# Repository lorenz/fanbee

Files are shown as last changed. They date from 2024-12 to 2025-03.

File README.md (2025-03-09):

# FanBee :honeybee:
*A Zigbee-controlled 140mm fan with electronically-controlled valve*

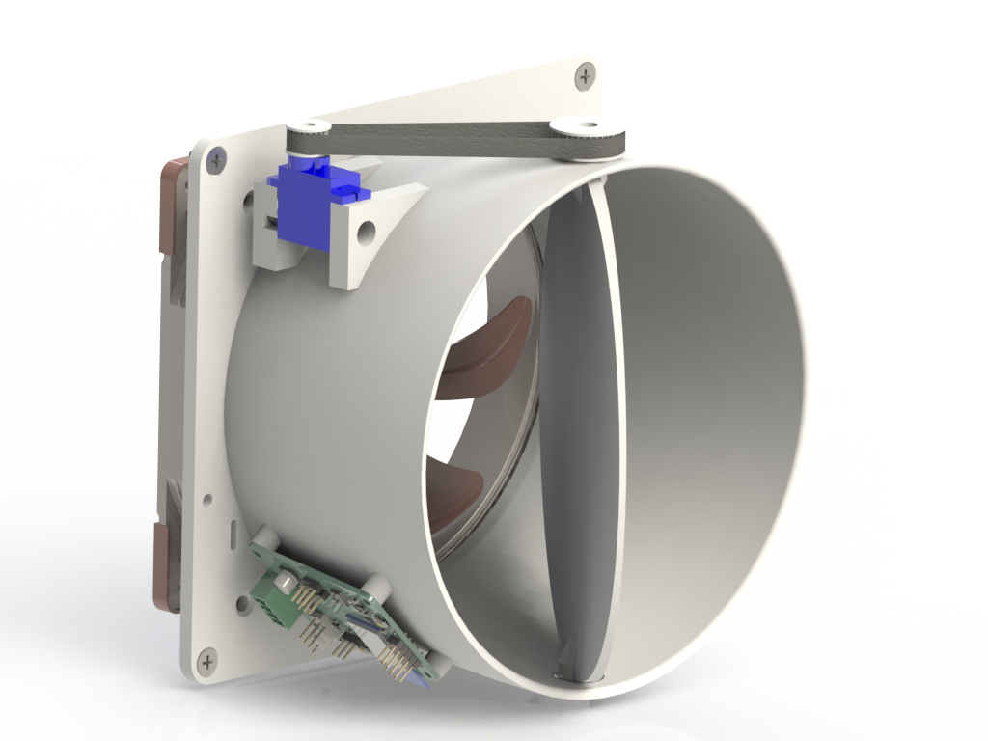
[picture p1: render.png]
Product Picture


Skip to the Build Guide if you want to know how to build one.

# Introduction

## User Interface
The small LED (D3) near the reset button indicates if the lowest (MCU) power
rail has power. If it is not illuminated nothing will happen, check power rails.

The firmware initially starts blinking its status LED (D4, near the JTAG
header) every 2 seconds, indicating that it is idle and is not connected to any
network. Press the Pair button after your ZigBee network is ready to join a new
device. The status LED will start to blink rapidly (every 0.5s) until it has
joined a network, then it will turn off.

Pressing the pair button while the device is already joined to a network will
result in two quick flashes of the status LED.

Long-pressing the pair button (>5s) will reset the device.

The last LED (D5) indicates if the fan is currently powered. It can be used
to diagnose fan or connectivity issues.

## Coordinator compatibility
Because the ZigBee HVAC fan device type is unfit for this device (it supports
various modes but no speed control) I've opted to implement it as a generic
level-controlled device (just like dimmable lights). This should give it fairly
broad coordinator compatibility.

There's a device model for the FanBee in Zigbee2MQTT which is what I'm
personally using to control them.

## Notes
* The power connector is designed for daisy-chaining, that's why there are
  two positive and negative positions. Only one of each needs to be connected
  for normal operation.
* Second Servo output is not used currently, was used in an earlier revision
  and left for any future use as there was space.
* SPI flash can be left unpopulated if you don't ever want to use OTA updates
  or maybe a later (larger) firmware. It's currently unused.
* Newer TI SDKs have been tested but drop off the Zigbee network for unknown
  reasons after hours or days. Use the pinned version.
* Make sure that the surface your're installing the base plate on is flat.
  Otherwise the bell shape gets distorted and the butterfly valve disk gets
  stuck. The tolerances there need to be relatively tight to not allow too much
  air to go through in closed state.

# Build Guide
## Requirements

### Off-the-shelf hardware
| Quantity | Part description |
| --- | --- |
| 8 | M3 brass heat-set inserts |
| 1 | M3 15mm buttonhead fastener |
| 1 | M3 10mm buttonhead fastener |
| 4 | M3 5mm fastener (ideally with integrated washer) |
| 4 | M4 countersunk fasteners for attaching the housing |
| 2 | 10x15x4mm ball bearings |
| 1 | SG90-compatible 180° servo |
| 1 | 140mm 24V or 12V PC-compatible PWM fan (plus screws if not included) |
| 30cm | 2GT timing belt (open-loop) |

This was designed for the Noctua NF-A14 industrialPPC-24V-3000 SP IP67 PWM, but
any other electrically-compatible 24V or 12V fans can be used. Note that the
power supply voltage needs to match the fan voltage, there is no regulator for
the fan power supply.

### PCB
The control PCB is custom-designed and can be ordered at your favorite PCB
manufacturer in various states of assembly. All SMT parts can be assembled
for relatively cheap by JLCPCB. One PCB is needed for each FanBee.

A OpenOCD and JTAG compatible programmer with a 2.45mm ARM 10 Pin JTAG
connector is required. This has been tested with a generic FT2232 board, but
a TI XDS110 or compatible LaunchPad should also work.

### Printed parts
The STLs for all printed parts are in the `parts` folder. One of each is
needed for a single fanbee.
`servo_pulley.stl` should be printed in resin or with a 0.2mm nozzle, the
rest of the parts do not need to be as precise.

## Assembly steps
1. Insert the 4 heat-set inserts into the studs for holding the PCB.
2. Insert the two heat-set inserts into the base for holding an optional PCB enclosure.
3. Insert a heat-set insert each into the bottom and top holes of the valve disk.
4. Press both ball bearings into their housings on the main part.
5. Place the fan at the back, route the wires through the slot and attach it with four fan screws.
6. Route the servo cables through the hole and attach the servo with two screws.
7. Attach the PCB with four 5mm screws.
8. Connect the 4-pin fan connector and 3-pin servo connector.
9. Place the fan disk between the bearings and push in the retaining pin from the bottom and the disk pulley from the top.
10. Secure the retaining pin with the 10mm M3 screw.
11. Secure the disk pulley with the 15mm M3 screw.
12. Push the servo pulley onto the servo and secure it with the provided screw.
13. Cut a sufficiently-long section of belt, loop it around the two servos and secure both ends with the belt retainer.
15. Attach the JTAG programmer and temporary power and flash the firmware.

## Future work
* Public CI for firmware and manufacturing files
* Render/photos of the finished product

# License
MIT for all the code I wrote as well as the CAD design files. Some code is also
related to TI's SimpleLink SDK (especially the generated syscfg), I don't claim
ownership of that, but TI grants you relatively broad permissions for most use.

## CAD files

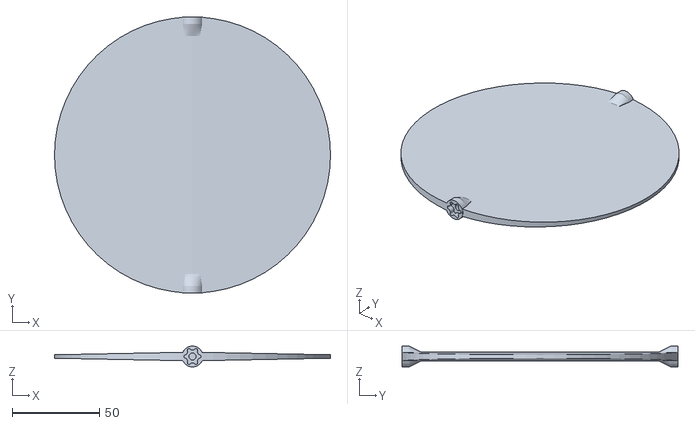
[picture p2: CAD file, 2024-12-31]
parts/valve_disk.stl
158.0 x 158.0 x 12.0

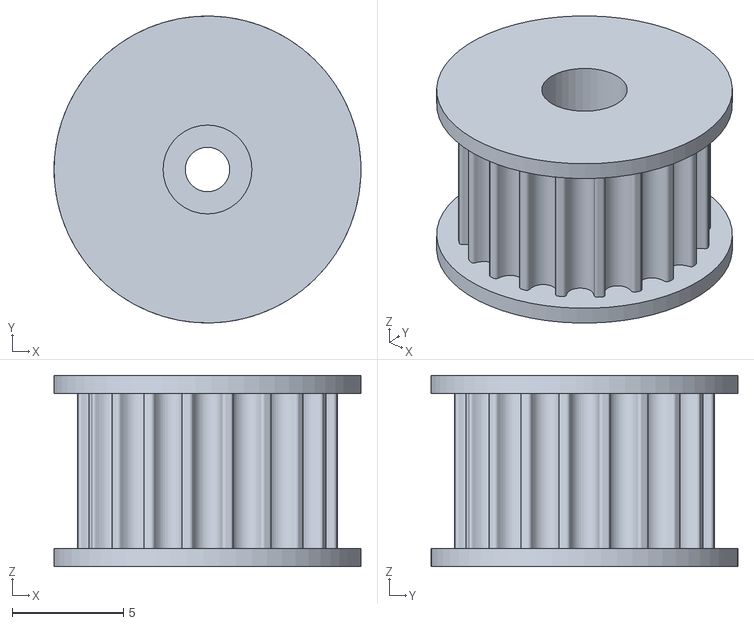
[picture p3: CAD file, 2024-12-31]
parts/servo_pulley.stl
13.8 x 13.8 x 8.60

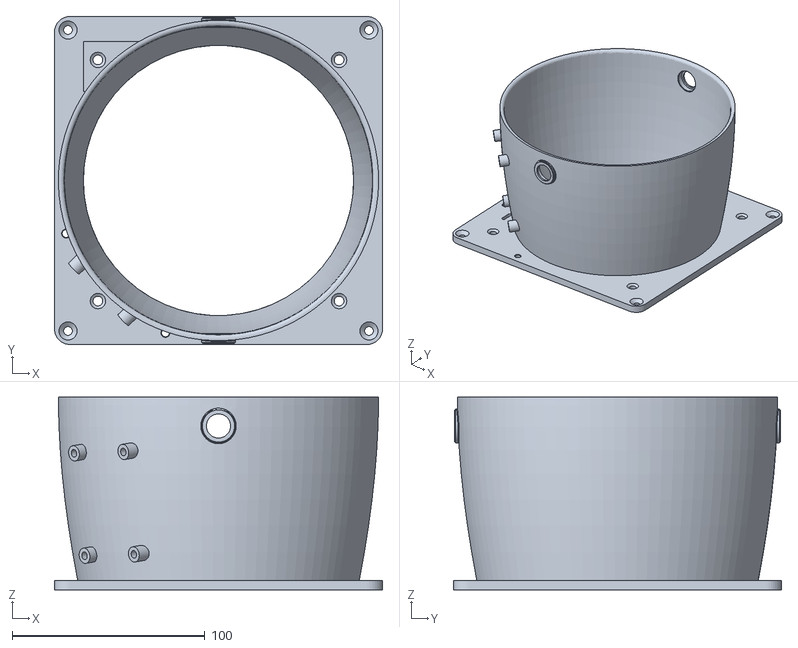
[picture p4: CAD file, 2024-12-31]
parts/housing.stl
170.0 x 170.0 x 100.0

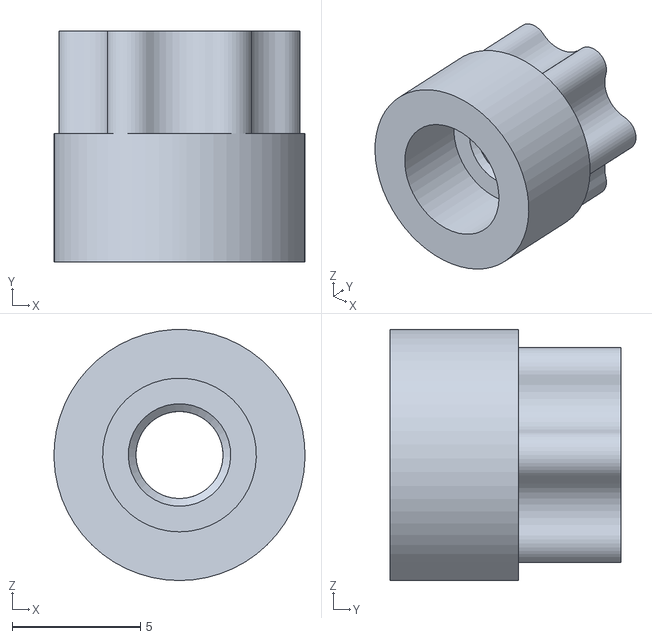
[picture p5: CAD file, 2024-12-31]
parts/retaining_pin.stl
9.80 x 9.00 x 9.80

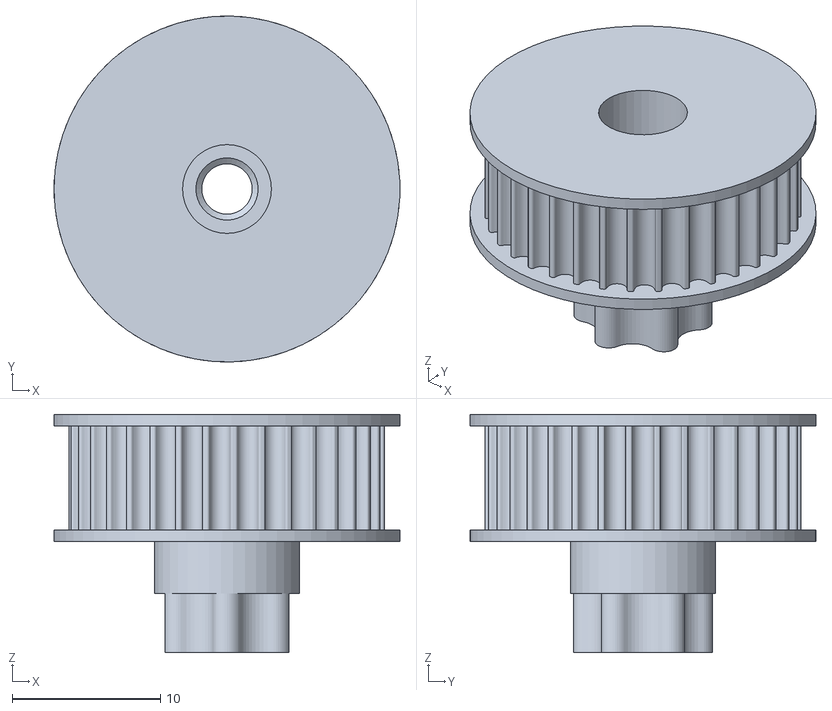
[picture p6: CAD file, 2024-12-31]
parts/disk_pulley.stl
23.4 x 23.4 x 16.1

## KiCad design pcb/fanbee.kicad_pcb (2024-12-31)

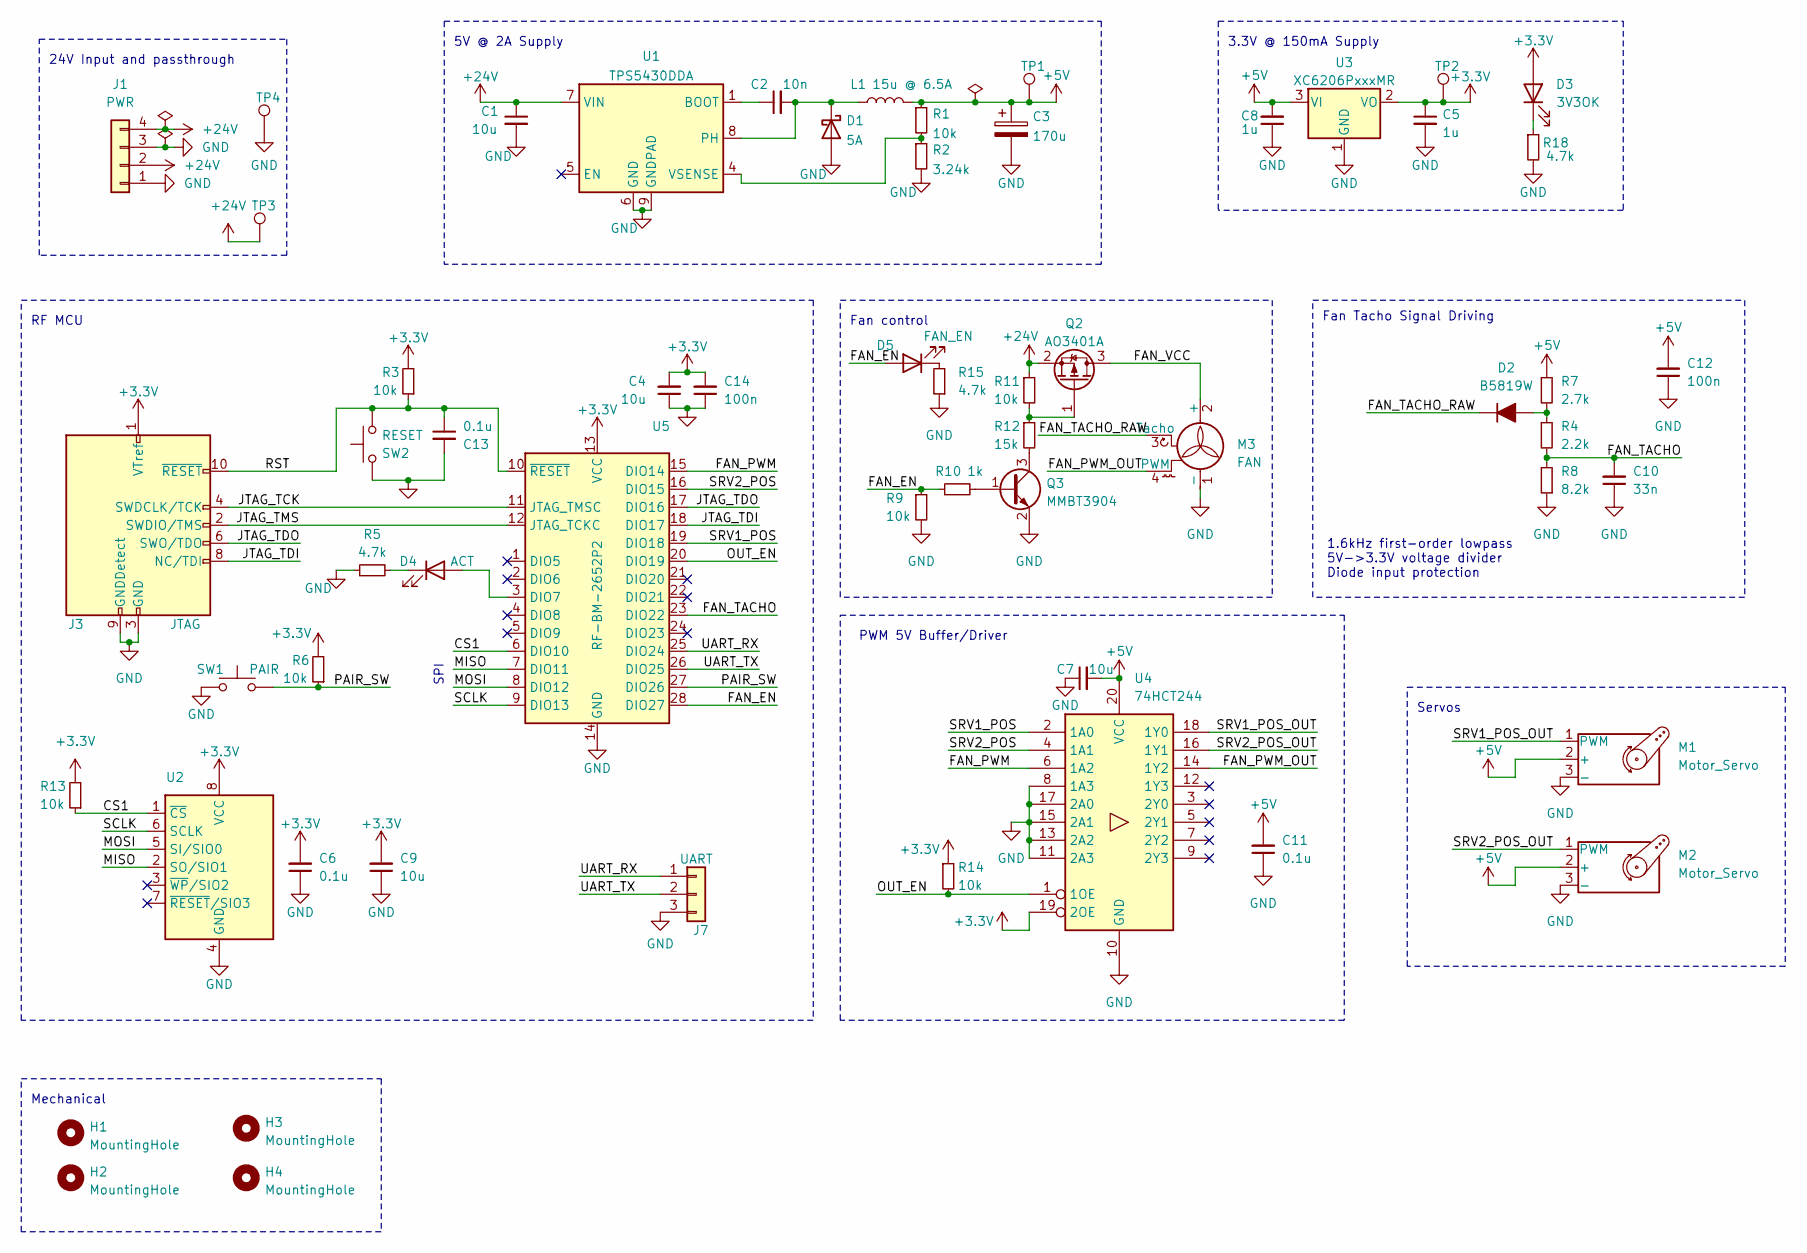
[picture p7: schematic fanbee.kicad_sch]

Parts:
C1, C4, C7, C9: 10u; C_0805_2012Metric; LCSC C440198
C2: 10n; C_0402_1005Metric; LCSC C15195
C3: 170u; CP_Elec_6.3x5.9; LCSC C311623
C5, C8: 1u; C_0805_2012Metric; LCSC C28323
C6, C11, C13: 0.1u; C_0402_1005Metric; LCSC C1525
C10: 33n; C_0603_1608Metric; LCSC C21117
C12, C14: 100n; C_0603_1608Metric; LCSC C14663
D1: 5A; D_SMA; LCSC C22452
D2: B5819W; D_SOD-123; LCSC C8598
D3: 3V3OK; LED_0805_2012Metric; LCSC C2297
D4: ACT; LED_0805_2012Metric; LCSC C2297
D5: FAN_EN; LED_0805_2012Metric; LCSC C2297
H1, H2, H3, H4: MountingHole; MountingHole_3.2mm_M3
J1: PWR; PhoenixContact_MCV_1,5_4-G-3.81_1x04_P3.81mm_Vertical; LCSC C8410
J3: JTAG; PinHeader_2x05_P2.54mm_Vertical; LCSC C7501276
J7: UART; PinHeader_1x03_P2.54mm_Vertical; LCSC C7501581
L1: 15u @ 6.5A; L_Sunlord_MWSA1004_11.5x10.5mm; LCSC C151872
M1, M2: Motor_Servo; PinHeader_1x03_P2.54mm_Vertical; LCSC C7501581
M3: FAN; FanPinHeader_1x04_P2.54mm_Vertical; LCSC C7501582
Q2: AO3401A; SOT-23; LCSC C15127
Q3: MMBT3904; SOT-23; LCSC C20526
R1, R3, R6, R9, R11, R13, R14: 10k; R_0402_1005Metric; LCSC C25744
R2: 3.24k; R_0402_1005Metric; LCSC C22994
R4: 2.2k; R_0402_1005Metric; LCSC C25879
R5, R15, R18: 4.7k; R_0402_1005Metric; LCSC C25900
R7: 2.7k; R_0603_1608Metric; LCSC C13167
R8: 8.2k; R_0402_1005Metric; LCSC C25924
R10: 1k; R_0402_1005Metric; LCSC C11702
R12: 15k; R_0402_1005Metric; LCSC C25756
SW1: PAIR; SW_SPST_TL3342; LCSC C318884
SW2: RESET; SW_SPST_TL3342; LCSC C318884
TP1, TP2, TP3, TP4: TestPoint; TestPoint_Pad_D1.0mm
U1: TPS5430DDA; TI_SO-PowerPAD-8_ThermalVias; LCSC C9864
U2: Macronix_USON8_EP_2x3_Pitch0.5mm; LCSC C152596
U3: XC6206PxxxMR; SOT-23-3; LCSC C5446
U4: 74HCT244; TSSOP-20_4.4x6.5mm_P0.65mm; LCSC C131088
U5: RF-BM-2652P2; LCSC C5440064

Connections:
+3.3V: C4.2, C5.1, C6.2, C9.2, C14.2, D3.2 (A), J3.1 (VTref), R3.2, R6.2, R13.2, R14.1, TP2.1, U2.8 (VCC), U3.2 (VO), U4.19 (2OE), U5.13 (VCC)
+5V: C3.1, C7.2, C8.2, C11.2, C12.2, L1.2, M1.2 (+), M2.2 (+), R1.1, R7.1, TP1.1, U3.3 (VI), U4.20 (VCC)
+24V: C1.1, J1.2, J1.4, Q2.2 (S), R11.1, TP3.1, U1.7 (VIN)
/CS1: R13.1, U2.1 (~CS), U5.6 (DIO10)
/FAN_EN: D5.2 (A), R9.1, R10.1, U5.28 (DIO27)
/FAN_PWM: U4.6 (1A2), U5.15 (DIO14)
/FAN_PWM_OUT: M3.4 (PWM), U4.14 (1Y2)
/FAN_TACHO: C10.2, R4.2, R8.2, U5.23 (DIO22)
/FAN_TACHO_RAW: D2.1 (K), M3.3 (Tacho)
/FAN_VCC: M3.2 (+), Q2.3 (D)
/JTAG_TCK: J3.4 (SWDCLK/TCK), U5.11 (JTAG_TMSC)
/JTAG_TDI: J3.8 (NC/TDI), U5.18 (DIO17)
/JTAG_TDO: J3.6 (SWO/TDO), U5.17 (DIO16)
/JTAG_TMS: J3.2 (SWDIO/TMS), U5.12 (JTAG_TCKC)
/MISO: U2.2 (SO/SIO1), U5.7 (DIO11)
/MOSI: U2.5 (SI/SIO0), U5.8 (DIO12)
/OUT_EN: R14.2, U4.1 (1OE), U5.20 (DIO19)
/PAIR_SW: R6.1, SW1.2, U5.27 (DIO26)
/RST: C13.1, J3.10 (~RESET), R3.1, SW2.1, U5.10 (~RESET)
/SCLK: U2.6 (SCLK), U5.9 (DIO13)
/SRV1_POS: U4.2 (1A0), U5.19 (DIO18)
/SRV1_POS_OUT: M1.1 (PWM), U4.18 (1Y0)
/SRV2_POS: U4.4 (1A1), U5.16 (DIO15)
/SRV2_POS_OUT: M2.1 (PWM), U4.16 (1Y1)
/UART_RX: J7.1, U5.25 (DIO24)
/UART_TX: J7.2, U5.26 (DIO25)
GND: C1.2, C3.2, C4.1, C5.2, C6.1, C7.1, C8.1, C9.1, C10.1, C11.1, C12.1, C13.2, C14.1, D1.2 (A), J1.1, J1.3, J3.3 (GND), J3.5 (GND), J3.9 (GNDDetect), J7.3, M1.3 (-), M2.3 (-), M3.1 (-), Q3.2 (E), R2.2, R5.1, R8.1, R9.2, R15.1, R18.2, SW1.1, SW2.2, TP4.1, U1.6 (GND), U1.9 (GNDPAD), U2.4 (GND), U2.EP (GND), U3.1 (GND), U4.8 (1A3), U4.10 (GND), U4.11 (2A3), U4.13 (2A2), U4.15 (2A1), U4.17 (2A0), U5.14 (GND)
unnamed: C2.2, D1.1 (K), L1.1, U1.8 (PH)
unnamed: D2.2 (A), R4.1, R7.2
unnamed: D3.1 (K), R18.1
unnamed: D4.2 (A), U5.3 (DIO7)
unnamed: D4.1 (K), R5.2
unnamed: D5.1 (K), R15.2
unnamed: Q2.1 (G), R11.2, R12.1
unnamed: Q3.1 (B), R10.2
unnamed: Q3.3 (C), R12.2
unnamed: C2.1, U1.1 (BOOT)
unnamed: R1.2, R2.1, U1.4 (VSENSE)

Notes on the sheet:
1.6kHz first-order lowpass 5V->3.3V voltage divider Diode input protection
RF MCU
SPI
Mechanical
Servos
5V @ 2A Supply
Fan Tacho Signal Driving
PWM 5V Buffer/Driver
24V Input and passthrough
Fan control
3.3V @ 150mA Supply

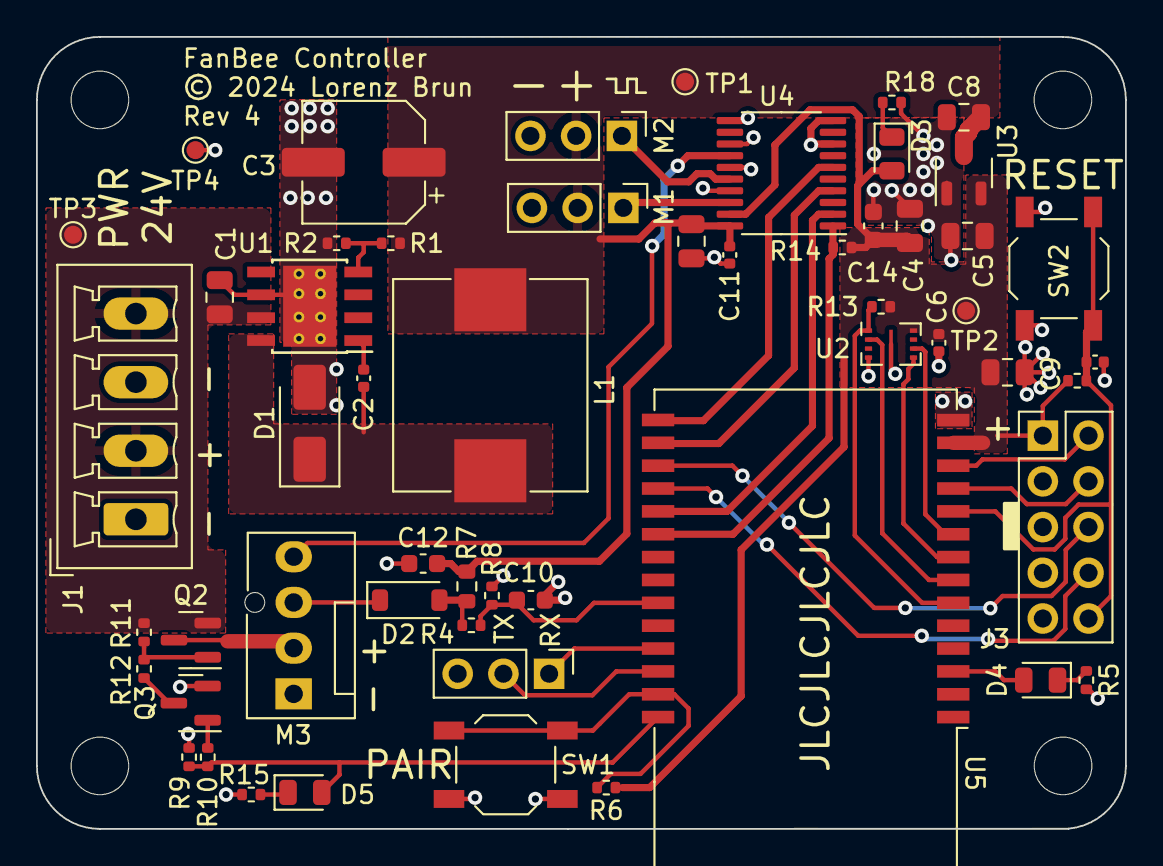
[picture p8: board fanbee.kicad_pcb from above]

Board: 2 copper layers, 60.5 x 44.0 mm, 59 parts (0 on the bottom side), 38 nets.

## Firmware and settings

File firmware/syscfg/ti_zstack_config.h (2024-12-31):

/*
 * Copyright (c) 2018, Texas Instruments Incorporated
 * All rights reserved.
 *
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
 * *  Redistributions of source code must retain the above copyright
 *    notice, this list of conditions and the following disclaimer.
 *
 * *  Redistributions in binary form must reproduce the above copyright
 *    notice, this list of conditions and the following disclaimer in the
 *    documentation and/or other materials provided with the distribution.
 *
 * *  Neither the name of Texas Instruments Incorporated nor the names of
 *    its contributors may be used to endorse or promote products derived
 *    from this software without specific prior written permission.
 *
 * THIS SOFTWARE IS PROVIDED BY THE COPYRIGHT HOLDERS AND CONTRIBUTORS "AS IS"
 * AND ANY EXPRESS OR IMPLIED WARRANTIES, INCLUDING, BUT NOT LIMITED TO,
 * THE IMPLIED WARRANTIES OF MERCHANTABILITY AND FITNESS FOR A PARTICULAR
 * PURPOSE ARE DISCLAIMED. IN NO EVENT SHALL THE COPYRIGHT OWNER OR
 * CONTRIBUTORS BE LIABLE FOR ANY DIRECT, INDIRECT, INCIDENTAL, SPECIAL,
 * EXEMPLARY, OR CONSEQUENTIAL DAMAGES (INCLUDING, BUT NOT LIMITED TO,
 * PROCUREMENT OF SUBSTITUTE GOODS OR SERVICES; LOSS OF USE, DATA, OR PROFITS;
 * OR BUSINESS INTERRUPTION) HOWEVER CAUSED AND ON ANY THEORY OF LIABILITY,
 * WHETHER IN CONTRACT, STRICT LIABILITY, OR TORT (INCLUDING NEGLIGENCE OR
 * OTHERWISE) ARISING IN ANY WAY OUT OF THE USE OF THIS SOFTWARE,
 * EVEN IF ADVISED OF THE POSSIBILITY OF SUCH DAMAGE.
 *
 */

/*
 *                           ti_zstack_config.h
 *
 *  DO NOT EDIT - This file was generated by the SysConfig tool.
 *
 *  Macros used to define a TI Z-Stack ZigBee device. New user defined
 *  options may be added to this file, as necessary.
 *
 */

#ifndef TI_ZSTACK_CONFIG_H
#define TI_ZSTACK_CONFIG_H

/* Default (primary) and secondary channel masks. Secondary mask is used when the
 * default channels fail.
 * Channels are defined in the following:
 *        11 - 26 : 2.4 GHz     0x07FFF800
 */
#ifndef DEFAULT_CHANLIST
#define DEFAULT_CHANLIST              0x02108800
#endif

#ifndef SECONDARY_CHANLIST
#define SECONDARY_CHANLIST            0x05ef7000
#endif

/* Define the default PAN ID.
 *
 * Setting this to a value other than 0xFFFF causes
 * ZDO_COORD to use this value as its PAN ID and
 * Routers and end devices to join PAN with this ID
 */
#ifndef ZDAPP_CONFIG_PAN_ID
#define ZDAPP_CONFIG_PAN_ID           0xFFFF
#endif

/* Specifiy whether to set the EPID to the Extended Address, or to use the
 * custom Extended Pan ID (EPID) defined by ZDAPP_CONFIG_EPID
 */
#ifndef SET_EPID_AS_EXT_ADDR
#define SET_EPID_AS_EXT_ADDR          TRUE
#endif

/* Define the default Extended Pan ID (EPID)
 * ZDAPP_CONFIG_EPID is only used if SET_EPID_AS_EXT_ADDR is FALSE. Otherwise,
 * the EPID is set to the Extended Address.
 */
#ifndef ZDAPP_CONFIG_EPID
#define ZDAPP_CONFIG_EPID             {0x01,0x23,0x45,0x67,0x89,0xAB,0xCD,0xEF}
#endif

/* in seconds; set to 255 to turn off route expiry */
#ifndef ROUTE_EXPIRY_TIME
#define ROUTE_EXPIRY_TIME             30
#endif

/*  Default indirect message holding timeout value:
 *  1-65535 (0 -> 65536) X CNT_RTG_TIMER X RTG_TIMER_INTERVAL
 */
#ifndef NWK_INDIRECT_MSG_TIMEOUT
#define NWK_INDIRECT_MSG_TIMEOUT      7
#endif

/* The number of simultaneous route discoveries in network */
#ifndef MAX_RREQ_ENTRIES
#define MAX_RREQ_ENTRIES              8
#endif

/* The maximum number of MAC frame transmission attempts allowed */
#ifndef ZMAC_MAX_FRAME_RETRIES
#define ZMAC_MAX_FRAME_RETRIES          3
#endif

/* Max number of times attempts looking for the next hop address of a message */
#ifndef NWK_MAX_DATA_RETRIES
#define NWK_MAX_DATA_RETRIES          2
#endif

/* The maximum number of times APS frames are retried after not receiving an APS ACK */
#ifndef APSC_MAX_FRAME_RETRIES
#define APSC_MAX_FRAME_RETRIES        3
#endif

/* This number is used by polled devices, since the spec'd formula
 * doesn't work for sleeping end devices.  For non-polled devices,
 * a formula is used. Value is in 2 milliseconds periods
 */
#ifndef APSC_ACK_WAIT_DURATION_POLLED
#define APSC_ACK_WAIT_DURATION_POLLED 3000
#endif

/* The maximum number of groups in the groups table */
#ifndef APS_MAX_GROUPS
#define APS_MAX_GROUPS                16
#endif

/* Number of entries in the regular routing table plus additional
 * entries for route repair
 */
#ifndef MAX_RTG_ENTRIES
#define MAX_RTG_ENTRIES               40
#endif

/* Maximum number of entries in the Binding table. */
#ifndef NWK_MAX_BINDING_ENTRIES
#define NWK_MAX_BINDING_ENTRIES       4
#endif

/* Default security key. */
#ifndef DEFAULT_KEY
#define DEFAULT_KEY                   {0x00,0x00,0x00,0x00,0x00,0x00,0x00,0x00,0x00,0x00,0x00,0x00,0x00,0x00,0x00,0x00}
#endif

/* ZigBee Alliance Pre-configured Distributed Link Key (for Distributed networks) */
#ifndef DISTRIBUTED_GLOBAL_LINK_KEY
#define DISTRIBUTED_GLOBAL_LINK_KEY   {0xD0,0xD1,0xD2,0xD3,0xD4,0xD5,0xD6,0xD7,0xD8,0xD9,0xDA,0xDB,0xDC,0xDD,0xDE,0xDF}
#endif

/* ZigBee Alliance Pre-configured TC Link Key - 'ZigBeeAlliance09' (for Centralized networks) */
#ifndef DEFAULT_TC_LINK_KEY
#define DEFAULT_TC_LINK_KEY           {0x5a,0x69,0x67,0x42,0x65,0x65,0x41,0x6c,0x6c,0x69,0x61,0x6e,0x63,0x65,0x30,0x39}
#endif

/* The number of milliseconds to wait between data request polls to the coordinator. */
#ifndef TXPOWER
#define TXPOWER                     15
#endif

/****************************************
 * The following are for End Devices only
 ***************************************/

/* Determine whether the radio on an End Device is always on */
#ifndef RFD_RX_ALWAYS_ON_CAPABLE
#define RFD_RX_ALWAYS_ON_CAPABLE            TRUE
#endif

#ifndef RFD_RX_ALWAYS_ON
#define RFD_RX_ALWAYS_ON                    TRUE
#endif

/* The minimum poll rate. */
#ifndef MINIMUM_APP_POLL_RATE
#define MINIMUM_APP_POLL_RATE                     100
#endif

/* The number of milliseconds to wait between data request polls to the coordinator. */
#ifndef POLL_RATE
#define POLL_RATE                     3000
#endif

/* This is used after receiving a data indication to poll immediately
 * for queued messages...in milliseconds.
 */
#ifndef QUEUED_POLL_RATE
#define QUEUED_POLL_RATE              100
#endif

/* This is used after receiving a data confirmation to poll immediately
 * for response messages...in milliseconds
 */
#ifndef RESPONSE_POLL_RATE
#define RESPONSE_POLL_RATE            100
#endif

/* This is used as an alternate response poll rate only for rejoin request.
 * This rate is determined by the response time of the parent that the device
 * is trying to join.
 */
#ifndef REJOIN_POLL_RATE
#define REJOIN_POLL_RATE              440
#endif

/* Maximum number of devices in the Assoc/Device list. */
#ifndef NWK_MAX_DEVICE_LIST
#define NWK_MAX_DEVICE_LIST           20
#endif

/* Total Number of APS keys that a TC can manage. This is equal to the number of devices a ZC can allow to join the network */
#ifndef ZDSECMGR_TC_DEVICE_MAX
#define ZDSECMGR_TC_DEVICE_MAX        3
#endif

/* Value used by end device when sending End Device Timeout Request */
/* This is an index into table timeoutValue[] defined in nwk_globals.c */
#ifndef END_DEV_TIMEOUT_VALUE
#define END_DEV_TIMEOUT_VALUE        8
#endif





/* Maximum size in bytes used by reportable attributes registered in any endpoint for the application (for analog attributes) */
#ifndef BDBREPORTING_MAX_ANALOG_ATTR_SIZE
#define BDBREPORTING_MAX_ANALOG_ATTR_SIZE                   4
#endif

/* Cluster Flags */
#define ZCL_SYSCONFIG
#define ZCL_READ
#define ZCL_WRITE
#define ZCL_DISCOVER
#define ZCL_BASIC
#define ZCL_IDENTIFY
#define ZCL_GROUPS
#define ZCL_SCENES
#define ZCL_ON_OFF
#define ZCL_LEVEL_CTRL
#define BDB_REPORTING


#endif /* TI_ZSTACK_CONFIG_H */

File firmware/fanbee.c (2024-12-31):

#include "fanbee.h"

#include <stdint.h>
#include <string.h>
#include <ti/display/Display.h>
#include <ti/drivers/NVS.h>
#include <ti/drivers/apps/Button.h>
#include <ti/sysbios/BIOS.h>
#include <ti/sysbios/family/arm/cc26xx/Timer.h>
#include <ti/sysbios/knl/Clock.h>
#include <ti/sysbios/knl/Semaphore.h>
#include <ti/sysbios/knl/Task.h>

#include "bdb_interface.h"
#include "cui.h"
#include "gp_common.h"
#include "nvintf.h"
#include "ota_client.h"
#include "ti_drivers_config.h"
#include "util_timer.h"
#include "zcl_config.h"
#include "zcl_ota.h"
#include "zcl_port.h"
#include "zcomdef.h"
#include "zstackapi.h"
#include "zstackmsg.h"

uint8 fanbee_Basic_ManufacturerName[] = {11, 'L', 'o', 'r', 'e', 'n', 'z', ' ', 'B', 'r', 'u', 'n'};
uint8 fanbee_Basic_ModelIdentifier[] = {7, 'F', 'a', 'n', 'B', 'e', 'e', '1'};
const enum8 DEFAULT_FANBEE_BASIC_POWER_SOURCE = POWER_SOURCE_DC;
const uint8 DEFAULT_FANBEE_LEVEL_CURRENT_LEVEL = 254;

// Semaphore used to post events to the application thread
static Semaphore_Handle appSemHandle;
static Semaphore_Struct appSem;

// App service ID used for messaging with stack service task
uint8_t sampleApp_serviceTaskId;

// App service task events, set by the stack service task when sending a message
static uint32_t appServiceTaskEvents;

// Passed in function pointers to the NV driver
static NVINTF_nvFuncts_t *nvm = NULL;

// Constants (TODO: Determine)
static const uint32_t valve_open = 2300;
static const uint32_t valve_closed = 600;

// Peripheral handles
static Display_Handle debug_display_handle;

static Button_Handle pair_btn_handle;

static LED_Handle act_led_handle;

static Clock_Handle tacho_clk_handle;
static Clock_Struct tacho_clk_struct;

static PWM_Handle pwm_fan = NULL;

static PWM_Handle pwm_srv1 = NULL, pwm_srv2 = NULL;

static bool joined = false;

// Functions for sample application setup
void sampleApp_task(NVINTF_nvFuncts_t *pfnNV);
static void fanbee_process_loop();
static void fanbee_initPeripherals();
static void fanbee_processZStackMsgs(zstackmsg_genericReq_t *pMsg);
static void fanbee_processAfIncomingMsgInd(zstack_afIncomingMsgInd_t *pInMsg);
static void fanbee_initZCLGeneral();
static void fanbee_ProcessCommissioningStatus(bdbCommissioningModeMsg_t *bdbCommissioningModeMsg);

// Update hooks
static void fanbee_updateOutputs();
static void fanbee_updateLevel();
static void fanbee_updateOnOff();

// Functions to process ZCL Foundation incoming Command/Response messages
static uint8_t fanbee_ProcessIncomingMsg(zclIncoming_t *pInMsg);

void Board_initHook(void) { PWM_init(); }

static NVINTF_itemID_t nvOnOffId = {
    .systemID = NVINTF_SYSID_APP,
    .itemID = FANBEE_NV_ONOFF,
    .subID = 0,
};
static NVINTF_itemID_t nvCurrentLevelId = {
    .systemID = NVINTF_SYSID_APP,
    .itemID = FANBEE_NV_CURRENT_LEVEL,
    .subID = 0,
};

// Application task entry point
void sampleApp_task(NVINTF_nvFuncts_t *pfnNV) {
  // Save and register the function pointers to the NV drivers
  nvm = pfnNV;
  if (nvm == NULL) {
    Display_printf(debug_display_handle, 0, 0, "No NVM available");
  }
  zclport_registerNV(nvm, ZCL_PORT_SCENE_TABLE_NV_ID);

  // Create semaphores for messages / events
  Semaphore_Params semParam;
  Semaphore_Params_init(&semParam);
  semParam.mode = ti_sysbios_knl_Semaphore_Mode_COUNTING;
  appSemHandle = Semaphore_construct(&appSem, 0, &semParam);
  sampleApp_serviceTaskId = OsalPort_registerTask(Task_self(), appSemHandle, &appServiceTaskEvents);

  fanbee_initPeripherals();

  // Initialize Zigbee
  fanbee_initZCLGeneral();
  gp_endpointInit(sampleApp_serviceTaskId);
  app_Green_Power_Init(sampleApp_serviceTaskId, &appServiceTaskEvents, appSemHandle,
                       FANBEE_GP_DATA_SEND_EVT, FANBEE_GP_EXPIRE_DUPLICATE_EVT,
                       FANBEE_GP_TEMP_MASTER_EVT);

  uint32_t onOffErr = NVINTF_NOTFOUND;
  uint32_t levelErr = NVINTF_NOTFOUND;
  if (nvm->readItem) {
    nvm->readItem(nvCurrentLevelId, 0, sizeof(fanbee_Level_CurrentLevel),
                  &fanbee_Level_CurrentLevel);
    nvm->readItem(nvOnOffId, 0, sizeof(fanbee_OnOff_OnOff), &fanbee_OnOff_OnOff);
  }

  if ((onOffErr == NVINTF_NOTFOUND) && nvm->createItem) {
    nvm->createItem(nvOnOffId, sizeof(fanbee_OnOff_OnOff), &fanbee_OnOff_OnOff);
  }
  if ((levelErr == NVINTF_NOTFOUND) && nvm->createItem) {
    nvm->createItem(nvCurrentLevelId, sizeof(fanbee_Level_CurrentLevel),
                    &fanbee_Level_CurrentLevel);
  }

  // Set up output state
  fanbee_updateOutputs();

  // Enable line driver IC outputs.
  GPIO_write(CONFIG_DRV_EN, 1);

  Display_printf(debug_display_handle, 0, 0, "Init done, starting loop");

  // No return from task process
  fanbee_process_loop();
}

static uint32_t fan_tacho_pulses = 0;
void fanbee_tachoCB(uint_least8_t index) { fan_tacho_pulses++; }

static void fanbee_tachoSumHandler() {
  appServiceTaskEvents |= FANBEE_TACHO_EVT;
  Semaphore_post(appSemHandle);
}

static void fanbee_pairButtonHandler(Button_Handle handle, Button_EventMask events) {
  if ((events & Button_EV_CLICKED) == Button_EV_CLICKED) {
    appServiceTaskEvents |= FANBEE_PAIR_EVT;
    Semaphore_post(appSemHandle);
  }
  if ((events & Button_EV_LONGCLICKED) == Button_EV_LONGCLICKED) {
    appServiceTaskEvents |= FANBEE_RESET_EVT;
    Semaphore_post(appSemHandle);
  }
}
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

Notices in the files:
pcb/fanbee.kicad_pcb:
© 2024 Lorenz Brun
